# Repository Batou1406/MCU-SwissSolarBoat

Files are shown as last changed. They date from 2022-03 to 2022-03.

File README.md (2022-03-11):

# MCU-SwissSolarBoat
written by : Baptiste Savioz, the 03.03.2022  
reviewed by : ..., the .. .. ....  
updaten by : ..., the .. .. ...  

# Introduction
This repository contains all required files and information for complete characterization of the main MCU-board of Swiss Solar Boat. Please read the documentation carefully before starting, especially the _Important things before starting_ section.

The main MCU-board is made of a powerfull microcontroller used for communication (based on the CAN protocol) between the differents modules of the boat. It also includes I2C lines with dedicated connectors for communication insides boat modules (eg. the battery box) and a SD card holder to save a logfile for example.

# ! Important things before starting !

# Documentation

## Sub-system characterization
### MCU
The board is based on [ATSAME51J20A-AF](https://www.mouser.ch/datasheet/2/268/60001507E-1660031.pdf) MCU from atmel, using the 32-bit ARM® Cortex®-M4 processor with Floating Point Unit (FPU). It is running at 120 [MHz] on 3.3[V].
* **Reset Pin** the reset pin is low active and powered-up trough a low pass RC filter as recommanded for design in noisy environnement. Moreover, it's connected to a push button for manual reset.
* **Power Pins** The power pins are wired according to typical power connection for switching mode power supply, with a feartite bead for high frequency isolation and EMC.
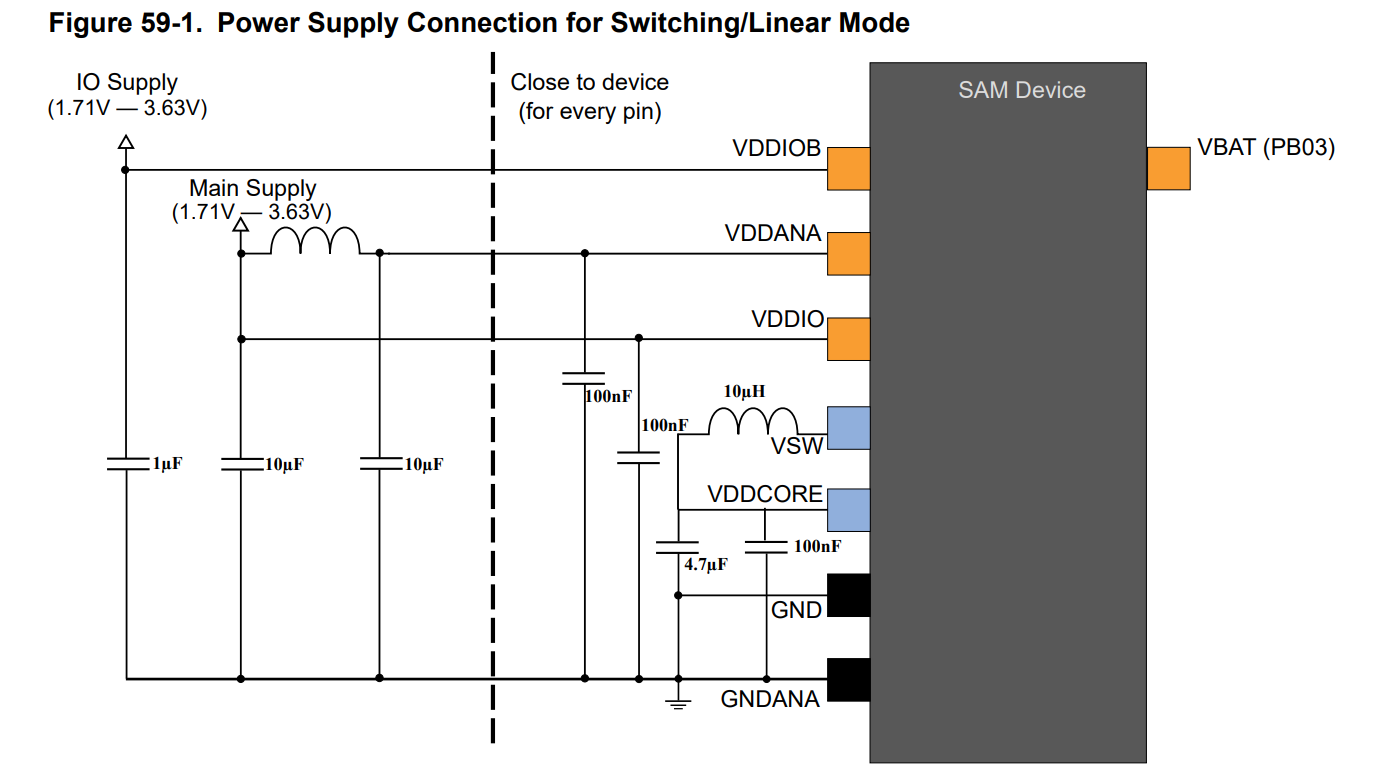
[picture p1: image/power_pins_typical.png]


### Power supply
The board is powered with a 24[V] DC line that goes all along the boat. It can be quite noisy and therefore we choosed to graduatly decreased the voltage from 24[V] to 5[V]  through a high efficiency buck converter and then from 5[V] to 3.3[V] with a LDO IC. The LDO will power only the main board to ensure stable and clean power to it. On the other hand, the 5[V] power supply can be used by the shield to power other small devices. 

 * **Buck converter** : 24[V] DC to 5[V] DC  
The buck used is the [TPS54233QDRQ1](https://www.ti.com/lit/ds/symlink/tps54233-q1.pdf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) from texas instrument. It has been designed with WEBENCH software from TI to operate at 20-28[V] in, 5[V] out, 2[A] out max, 50[°C].  
https://webench.ti.com/power-designer/switching-regulator?powerSupply=0



 * **LDO** : 5[V] DC to 3.3[V] DC    
 The LDO used is the [AP7365-33WG-7](https://www.diodes.com/assets/Datasheets/products_inactive_data/AP7365.pdf), which is a fixed output voltage LDO in the package SOT25. It not recommanded for new design and will shortly full out of supply. The newer version AP7366 is available but haven't been choosen because parts weren't available for now. However, switching to AP7366 wouldn't required adaptation of the PCB since it is also in the SOT25 package. Further update of this PCB may want to upgrade the LDO to an up to date version.

### Clock
The MCU has several clocking options and can admit two external oscillators (32768[Hz] for real time counting applications RTC and higher frequency oscillators). By default it is running at 48[MHz] on internal oscillators. Only the RTC oscillators is mounted on the board. It is a 32768[Hz] oscillators with low load capacitance (9[pF]) [Q 0,032768-JTX310-9-20-T1-HMR-LF](https://www.jauch.com/downloadfile/57fde22d50dbf_d3c203011c87952f2834/jtx310-auto-2-210512.pdf) connected to pin PA0 and PA1 (XIN32, XOUT32).
Hz
### Communication
* **CAN** : The MCU comes with two built-in CAN controller which will be both used. The CAN tranciever [TCAN337GDR](https://www.ti.com/lit/ds/symlink/tcan337g.pdf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) is used to handle the CAN protocol. It's 3.3V logic, therefore the differential on the CAN bus is 3.3V. Nonetheless, the device is fully compatible with 5V differential logic. The CAN tranciver uses a serial line to communicate with the CAN controller of the MCU. m Moreover it also inlcudes a silent mode for listen only (high active) and a fault pin to indicate a failure on the device (high active). In order to use the silent mode, a solder bridge need to be fill on the board, otherwise, if silent mode is of no use, please use the other solder bridge to ground it. The fault pin needs a pull-up resistor to be mounted on the board and the solder bridge to be filled in order to be used.  Furthermore, the CAN lines are available through a [JST-S04B-PASK-2-LF-SN](https://datasheet.octopart.com/S04B-PASK-2%28LF%29%28SN%29-JST-datasheet-1807.pdf) connector (4 pins - 2mm pitch). Ground and 24V supply voltage must be connected through jumpers. One must be extra careful when connecting them to avoid connecting two differents power supply together (risk of BOUM) or different supply than 24[V], and also when connecting the ground to avoid ground loop.

|Name|Pin connected on the MCU|comment|
|----|---|---|
|RX_CAN0|PA23||
|TX_CAN0|PA22||
|S_CAN0|PA21|a solder bridge needs to be filled if one wants to connect this pin to the MCU, otherwise another solder bridge needs to be filled in order to ground it|
|FAULT_CAN0|PA20|A pull-up resistor needs to be mounted and a solder bridge to be filled if one wants to connect this pin to the MCU|
|RX_CAN1|PB15||
|TX_CAN1|PB14||
|S_CAN1|PA15|a solder bridge needs to be filled if one wants to connect this pin to the MCU, otherwise another solder bridge needs to be filled in order to ground it|
|FAULT_CAN1|PA14|A pull-up resistor needs to be mounted and a solder bridge to be filled if one wants to connect this pin to the MCU|

* **I2C** : The MCU comes with 8 SERCOM lines, that can be configured for serial communication protocol such as UART, I2C, RS232, RS485, SPI. Please carefuly check the documentation before configuring one of these protocol, they require dedicated SERCOM port. Section 6.2.8.1 may be handy. Moreover, not all SERCOM port can be used for I2C communication. The pins that support I2C communication for a 64 pins package are :  
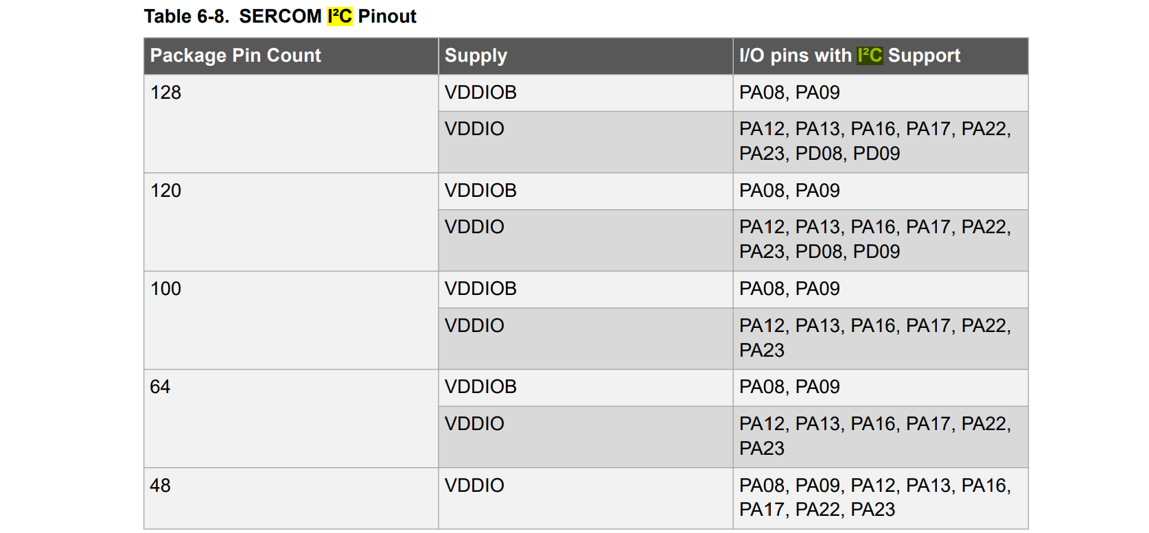
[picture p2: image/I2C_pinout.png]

the MCU-board comes with one dedicated I2C line. Another line has been left free for that pruposes but there is no connector mounted on the board by default. Other I2C pins than those listed below are already used for other tasks (CAN, SD-card) and aren't available anymore.

|Name|Pin connected on the MCU|comment|
|----|---|---|
|SDA_0|PA16||
|SCL_0|PA17||  
|SDA_1|PA13|*no connector mounted on the main-MCU board, a dedicated shield is necessary to use that line*|
|SCL_1|PA12|*no connector mounted on the main-MCU board, a dedicated shield is necessary to use that line*|  

It's available through a [JST-S04B-PASK-2-LF-SN](https://datasheet.octopart.com/S04B-PASK-2%28LF%29%28SN%29-JST-datasheet-1807.pdf) connector (4 pins - 2mm pitch). The power supply line is at 3.3[V] and is connected to the connector through a jumper. It must absolutely be deconnected if pluged to a device with its own power supply (even if it's 3.3[V]). Moreover, one must be careful when connecting the ground, in order to avoid ground loop.

* **JTAG** : The MCU has a JTAG debugging standard built-in. The connections is made through a 10 (2x5) male pin headers connector with 1.27[mm] pitch : [FTSH-105-01-L-DV-K](http://suddendocs.samtec.com/catalog_english/ftsh_smt.pdf).  
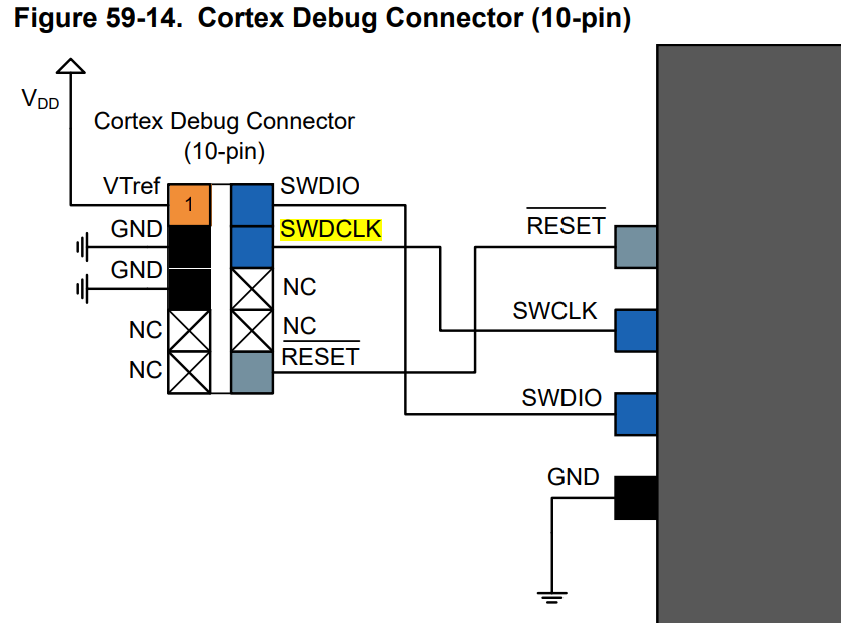
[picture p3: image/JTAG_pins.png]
JTAG_oins JTAG_pins

 
* **USB** : the MCU has a built-in USB 2.0 line. In order to be used the MCU need to be powered at 3.3[V] (min 3[V] - max 3.6[V]) and there is some restrictions on clock source and frequency, especially for USB host connections, that need to be taken into account when doing the firmware. A micro-USB B connector has been choosen for that connection. The VBUS line (5[V]) is of no use on the board and it is not further connected. The ID pin from the micro-USB B connector is by default left unconnected but there is a solder bridge jumper available on the board if it needs to be grounded (in order to host USB communication).

### Connectors
- complete list of connectors

### SD-card and memory
An SD slot is available on the board and it is handle by the SDHC0 line of the MCU. It's powered at the 3.3[V] by the LDO. Please be careful and read the dedicated documentation when designing an SD application, especially about the oprating voltage.

|Name|Pin connected on the MCU|comment|
|----|---|---|
|SDHC0 DAT0|PA09||
|SDHC0 DAT1|PA10||
|SDHC0 DAT2|PA11||
|SDHC0 DAT3|PB10||
|SDHC0 CMD|PA08||
|SDHC0 CLK|PB11||
|SDHC0 CD|PA06||
|SDHC0 WP|PA07||

## exhaustive list of component
|Component|name|number|reference|general purpose|usual reseller|link|
|---|----|---|---|---|---|----|
|Microcontroler|ATSAME51J20A-AF|1|CMP-002-000002-1|MCU of the board|Mouser|https://www.mouser.ch/ProductDetail/Microchip-Technology-Atmel/ATSAME51J20A-AF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|
|Buck|---|1|---|Power supply : convert 24V DC to stable 5V DC|---|
|LDO|---|1|---|Power supply : convert 5V DC to stable 3.3V DC|---|
|Crystal|---|1|---|Frequency generation for the MCU|---|

## Pinout and Shield
pinout schematic and shield characterization

## physical adress of modules
|Module|protocol|Address|general purpose|
|---|---|---|---|
|dummy|I2C|0xfh6c|dummy module used for example|

 Repository for documentation, characteristics and all required elements for the Microcontroller board, including PCB conception, of SSB.

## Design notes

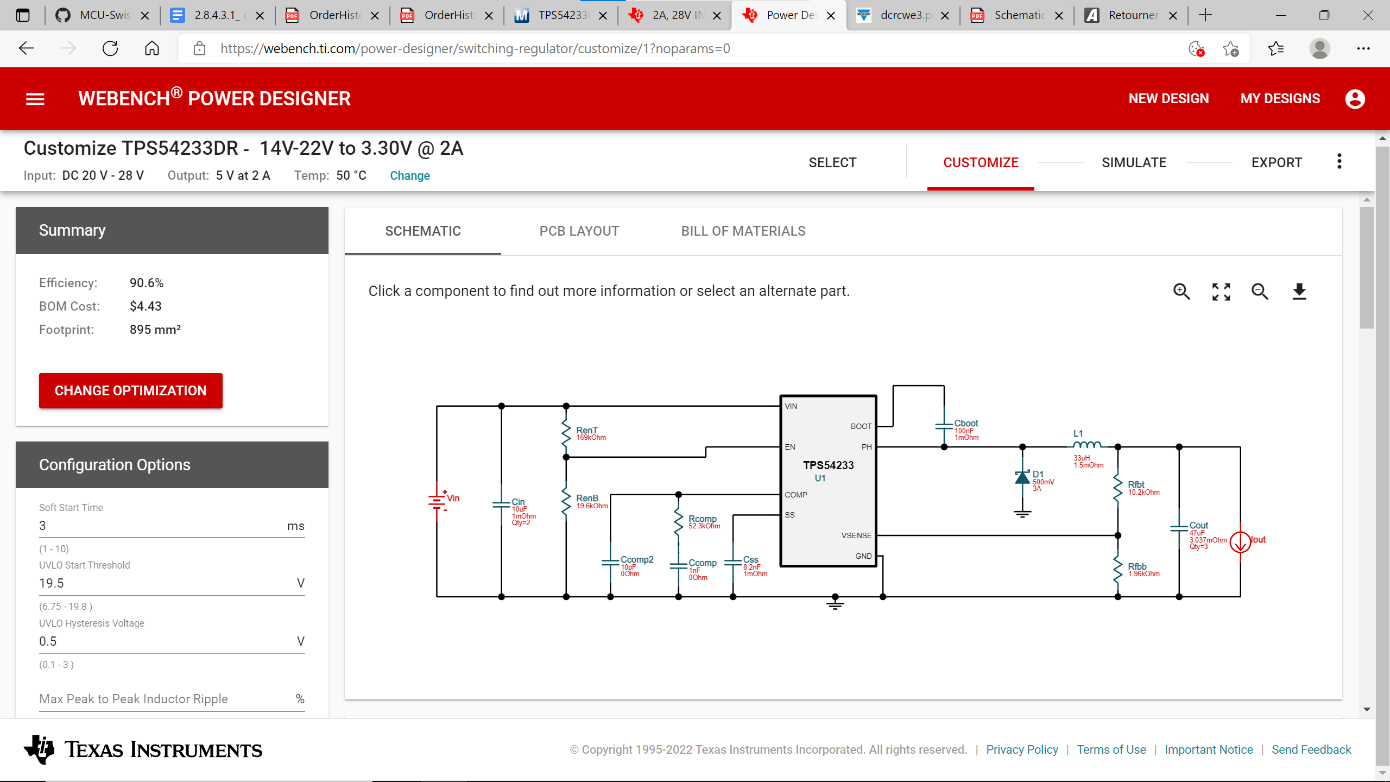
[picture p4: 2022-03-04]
image/schema buck.png

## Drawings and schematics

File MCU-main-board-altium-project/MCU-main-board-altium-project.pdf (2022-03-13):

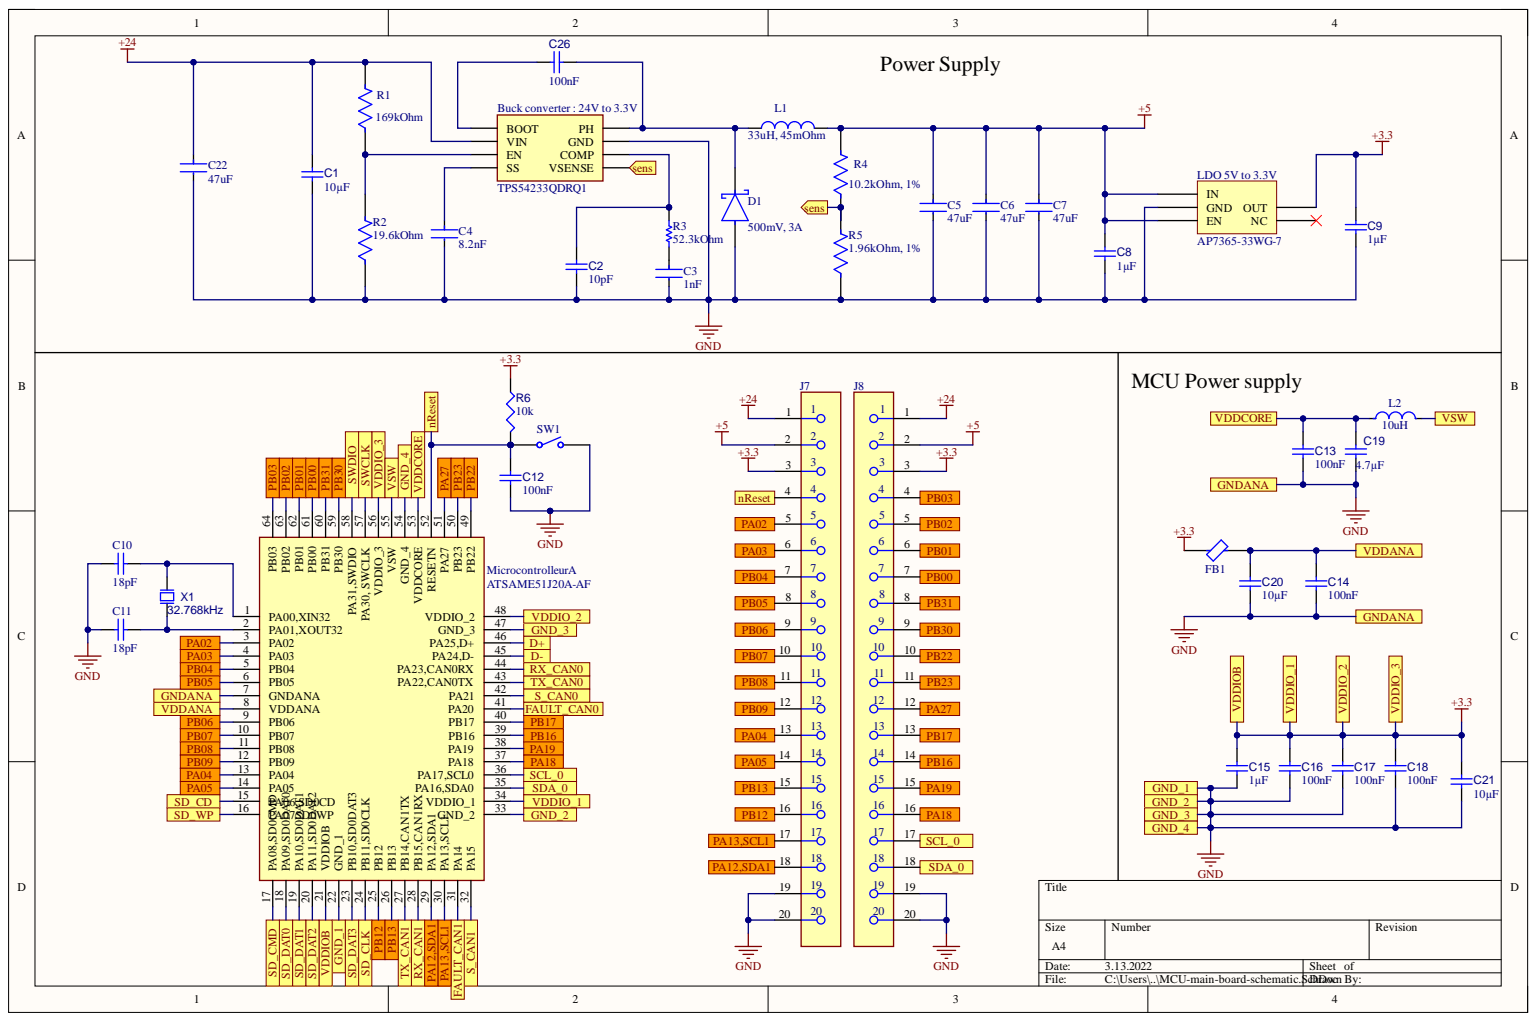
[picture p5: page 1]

sens

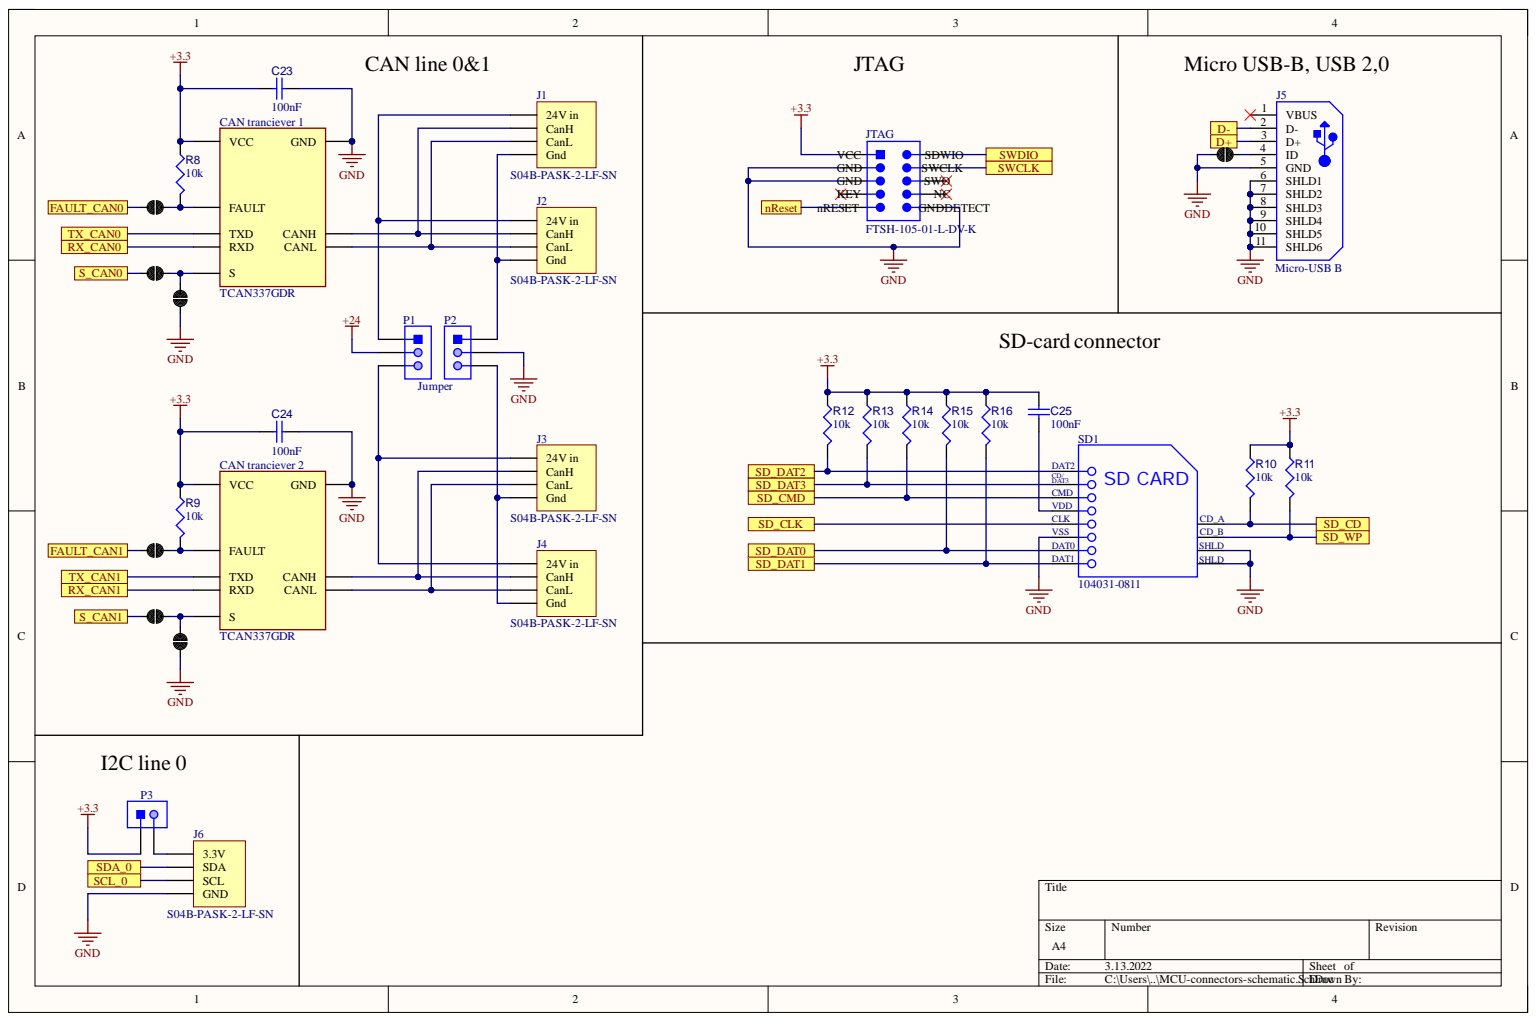
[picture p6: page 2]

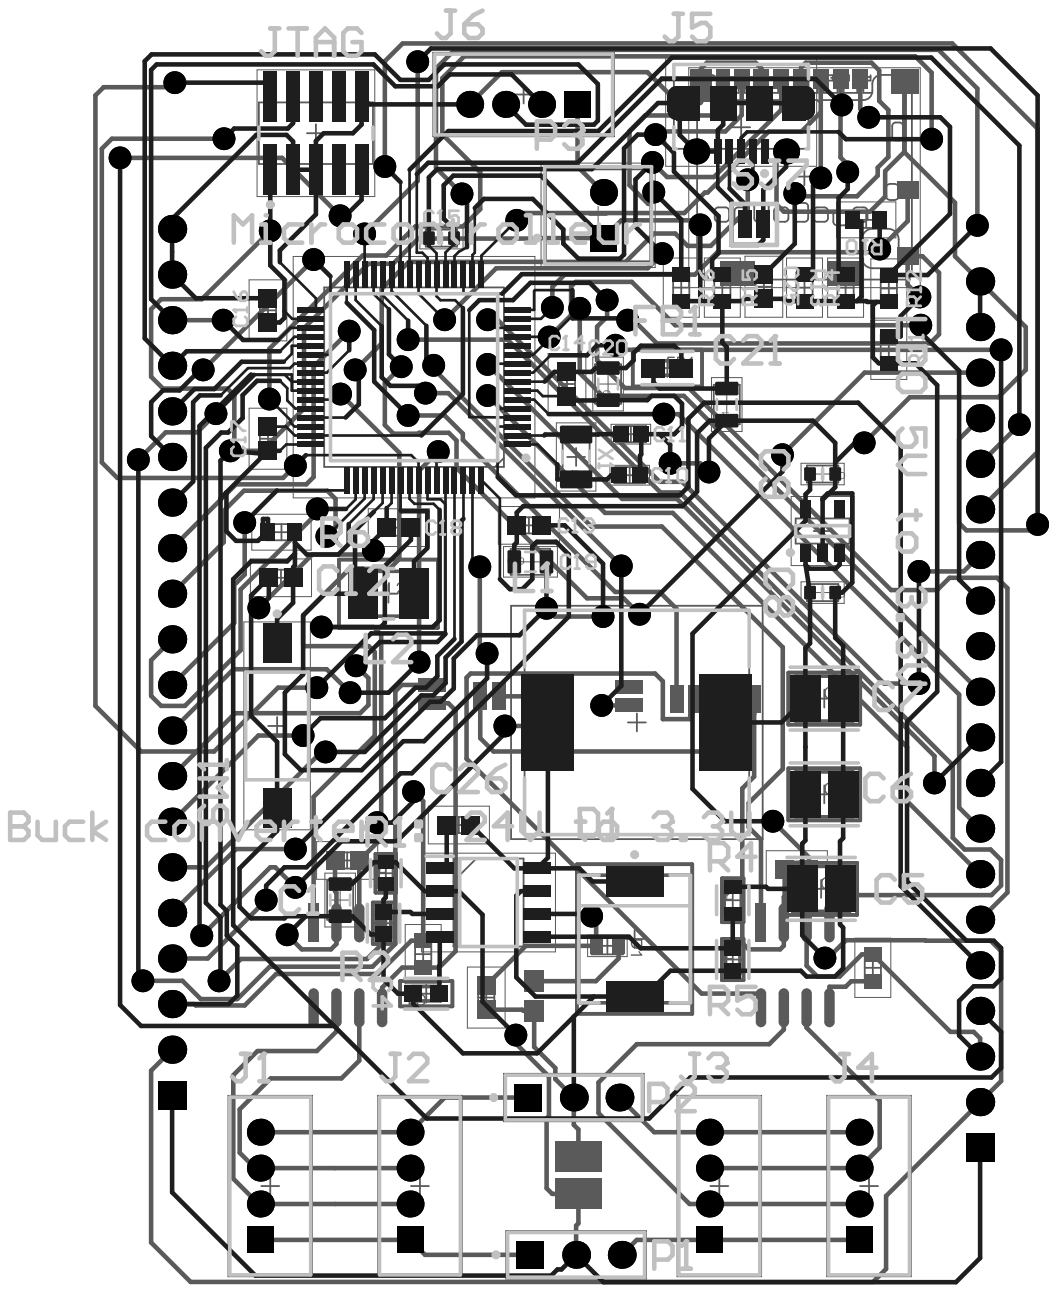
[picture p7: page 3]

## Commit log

2022-03-04 buck design
    [MCU-main-board-altium-project.PrjPcb, MCU-main-board-schematic.SchDoc]
2022-03-06 update power pins
    [MCU-main-board-altium-project.PrjPcb, MCU-main-board-schematic.SchDoc]
2022-03-06 update USB and CAN
    [MCU-main-board-altium-project.PrjPcb, MCU-main-board-schematic.SchDoc]
2022-03-07 update CAN
    [MCU-connectors-schematic.SchDoc, MCU-main-board-schematic.SchDoc]
2022-03-08 CAN correction and power
    [MCU-connectors-schematic.SchDoc, MCU-main-board-altium-project.PrjPcb, MCU-main-board-schematic.SchDoc]
2022-03-08 update CAN and JTAG
    [MCU-connectors-schematic.SchDoc, MCU-main-board-schematic.SchDoc]
2022-03-11 update component to 0603 package
    [MCU-connectors-schematic.SchDoc, MCU-main-board-altium-project.PrjPcb, MCU-main-board-schematic.SchDoc]
2022-03-11 pinout correction
    [MCU-connectors-schematic.SchDoc, MCU-main-board-schematic.SchDoc]
2022-03-11 final schematic
    [MCU-connectors-schematic.SchDoc, MCU-main-board-schematic.SchDoc]
2022-03-11 PCB layout start
    [MCU-connectors-schematic.SchDoc, MCU-main-board-PCBPcbDoc.PcbDoc, MCU-main-board-altium-project.PrjPcb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]
2022-03-13 PCB first routing
    [MCU-connectors-schematic.SchDoc, MCU-main-board-PCBPcbDoc.PcbDoc, MCU-main-board-altium-project.PrjPcb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]
